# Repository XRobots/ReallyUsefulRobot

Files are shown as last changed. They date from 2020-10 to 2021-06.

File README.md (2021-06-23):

# ReallyUsefulRobot

## Hardware

CAD files are provided in STEP/STP format. This is the whole assembly as a solid format so you can easily edit it. You will need to load it into some CAD software and edit/export individual STLs for printing.

Tyres are printed in TPU, I used Ninjaflex. The rest in PLA printed with a combination of 0.5mm and 1.2mm nozzles.

Motors are 6374 150Kv BLDC motors from the ODrive store: https://odriverobotics.com/shop
Encoders and cables are the 8192 CPR encoders also from the ODrive store.
I used a 56V ODrive 3.6, the robot runs from a 24V LiPo, but it can be 25V+ when it's charged.
Wheel Drive belts are 590mm T5 12mm wide PU belts with steel tensioners made by Synchroflex.
'Utility Stick' drive belt is an HTD 5mm pitch 15mm wide 1790mm length belt.

Other electronics so far include:

-Teensy 4.1
-NVIDIA Xavier NX
-RPLIDAR A2
-24v and 11.1v lipos, switches and wiring etc

## Software

Obviously this isn't a comprehensive guide to ROS, you will need to undestand some core concepts before building this. The Robot runs ROS Melodic on Ubuntu 18.04. This is because the NVIDIA Xavier NX runs 18.04 by default.

On the robot:

The arduino code runs on the Teensy 4.1. This talks to the wheel encoders. It subscribres to the cmd_vel topic and publishes Odom, and TF for the robot's motions. The RPLIDAR A2 node publishes the scan topic: https://github.com/robopeak/rplidar_ros

The Teensy also talks to the ODrive on Serial1. In order to get the ROS Serial library running on the Teensy 4.1, and get both the ROS Serial library and the ODrive library to run together I had to make various modifications. I removed mentions of the Stream Operator which were in the original ODrive Arduino example: https://github.com/madcowswe/ODrive/tree/master/Arduino/ODriveArduino/examples/ I also had to modify the ROS Serial library to add Teensy 4.1 support, and increase buffers so that the Odom message could be published over Serial. I've included both modified libraries as zip files.

The 'rur' and 'rur_description' ROS packages are installed on the robot, and everything is launched with the 'rur_bringup.launch' file. This launches the ROS Serial node to talk tot he Teensy 4.1, starts the laser, and also uses the Robot & Joint State Publishers to publish the transform in the URDF file so the laser is linked to the robot base in the right place.

On my remote workstation:

The 'rur_navigation' ROS package is installed on the remote workstation (although it could be run locally). You will also need to install the ROS navigation stack and slam_gmapping. You will also need to run rosdep to install any other dependencies: http://wiki.ros.org/rosdep

https://github.com/ros-planning/navigation/tree/melodic-devel
https://github.com/ros-perception/slam_gmapping/tree/melodic-devel

There is no launch file for gmapping, so having launched the rur_bringup package on the robot and launched Gmapping ( rosrun gmapping slam_gmapping scan:=scan ) you'll have to open Rviz and manually add/connect the topics for TF/Laser/Map etc. You can use the map server/saver command to save the map ( rosrun map_server map_saver -f ~/map )

After the map is complete you can launch the rur_navigation package which will open Rviz automatically. Use: roslaunch rur_navigation rur_navigation.launch map_file:=$HOME/map.yaml   to connect to the map you saved.

## Simulation

> **_NOTE:_** The following content in the README includes implementation and documentation of Simulation package of ReallyUsefulRobot and is being made by [Pranshu Tople](https://youtube.com/PranshuTople) and is been documented LIVE on his [YouTube Playlist](https://youtube.com/playlist?list=PLFnCFnTZNyU8-omA_VFztWfeFn2gCyY4_). James Bruton is not responsible if the following simulation package has any issues. So if face any problem in simulation, you can open up a GitHub Issue and tag [Pranshu Tople's Github Account](https://github.com/PranshuTople). Hope you enjoy Simulating ReallyUsefulRobot on your PC ☺️✌🏼

<p>
<a href="https://youtu.be/o7w7yv-Nros">
Fusion2URDF</a>
<a href="https://youtu.be/ufYxkNnEFYw">
Teleoperation & Gazebo Plugins</a>
<a href="https://youtu.be/lZVa8o1yxz0">
Mapping in Simulation</a>
<a href="https://youtu.be/DU31PuQjK-I">
Navigation in Simulation</a>
</p>

You don't have to worry anymore if you don't have enough capital to build the RUR robot! You can simply follow the guide given below, and you will have simulation of RUR running on your PC without any issue. The simulation works exactly like the real robot and communicates on the same topic lists. So if you make some software or package for simulated robot, the same would work on real RUR robot without any problem. This opens up gates for the Open-Source community to build various different applications around RUR.

### Downloading Pre-requisites

If you have not downloaded the full-desktop-version of ROS which comes with Gazebo Simulator, then you might need to download a couple of pre-requisites to run the simulation. Even if you have downloaded the full version, yet its a good practice to run the following command which checks if all the pre-requisites are installed or not. And if they are not installed, then the same command downloads them all automatically.

```
sudo apt-get install gazebo9 libgazebo9-* ros-melodic-robot-state-publisher ros-melodic-robot-joint-state-publisher ros-melodic-robot-joint-state-publisher-gui ros-melodic-teleop-twist-keyboard ros-melodic-gmapping ros-melodic-slam-gmapping ros-melodic-map-server
```

### Testing the simulation

Firstly, please place this complete repository or just the ROS folder into your src folder of [catkin_ws](http://wiki.ros.org/catkin/Tutorials) and run catkin_make command. Once the catkin_make is done successfully, then to launch the robot in an empty simulation world for testing in Gazebo Simulator, run the following command on your terminal

```
roslaunch rur_detailed_description gazebo.launch
```
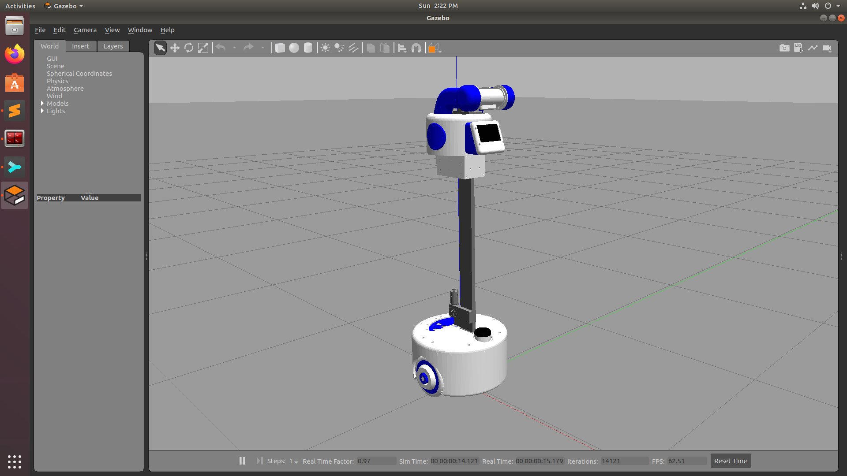
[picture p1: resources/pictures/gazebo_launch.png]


Once you have successfully launched the simulation, you can also run the Teleop node to teleoprate you robot using keyboard. To run the node, paste the following command in a new terminal and you can move your robot around using ' i ' ,' j ' , ' k ' , ' l ' , ' , '<br>
* i = move forward
* k = stop
* j = rotate left
* l = rotate right
* , = move backward
* along with few more operations like 'u','o','m','.' to go forward-left, forward-right, backward-left and backward-right respectively

```
rosrun teleop_twist_keyboard teleop_twist_keyboard.py
```
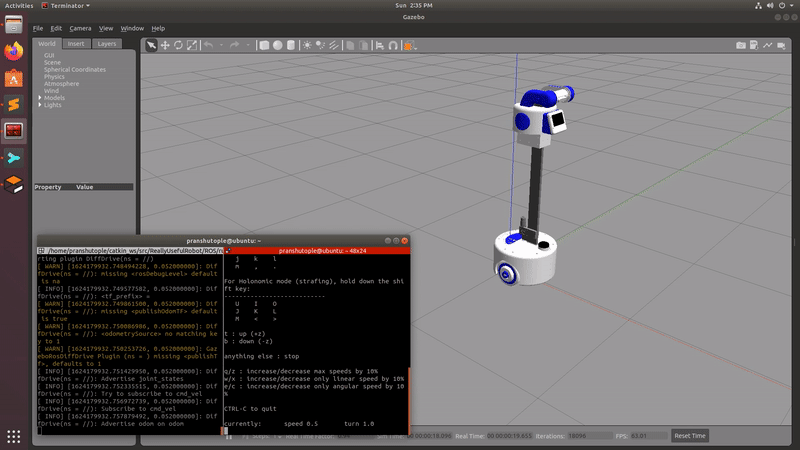
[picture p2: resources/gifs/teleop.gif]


You can also add a couple of obstacles in the environment and check if the LiDAR is able to detect them. Just run the following command and it will open up RViz which is a robot visualization tool that helps you visualize sensor data from the robot.
```
roslaunch rur_detailed_description display.launch
```
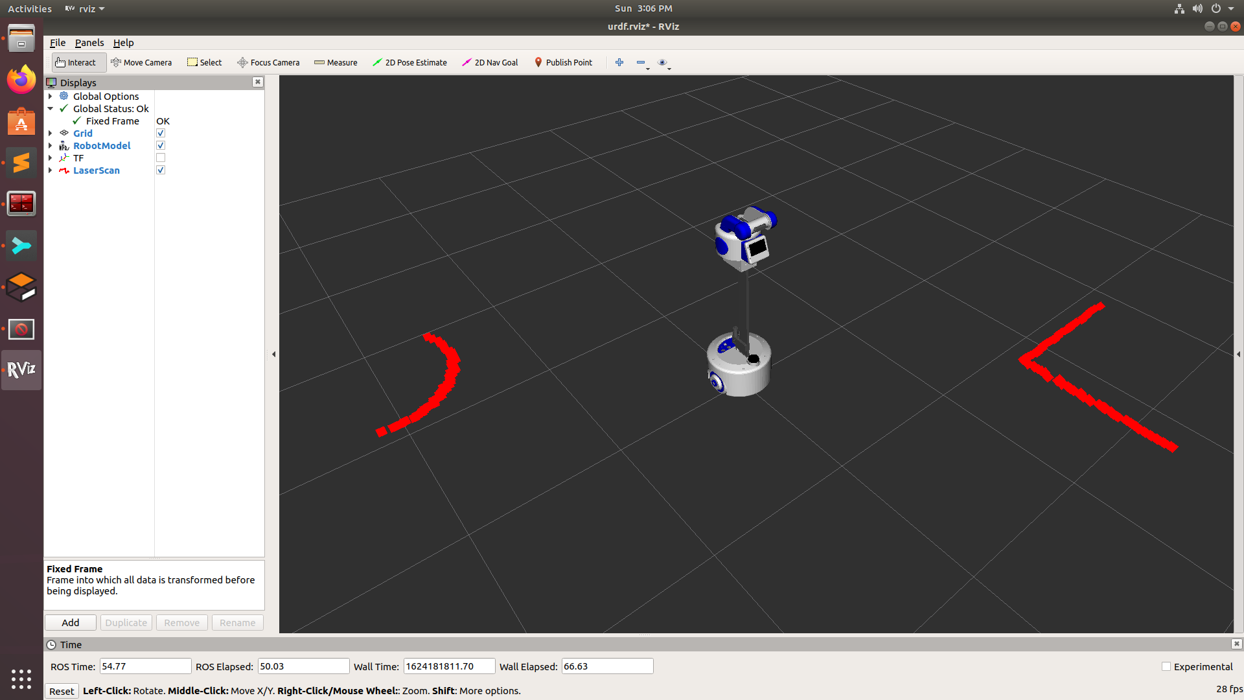
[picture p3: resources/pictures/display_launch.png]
 

RViz is also a place where you can closely inspect the URDF of the robot and look at the detailed TF structer of the robot

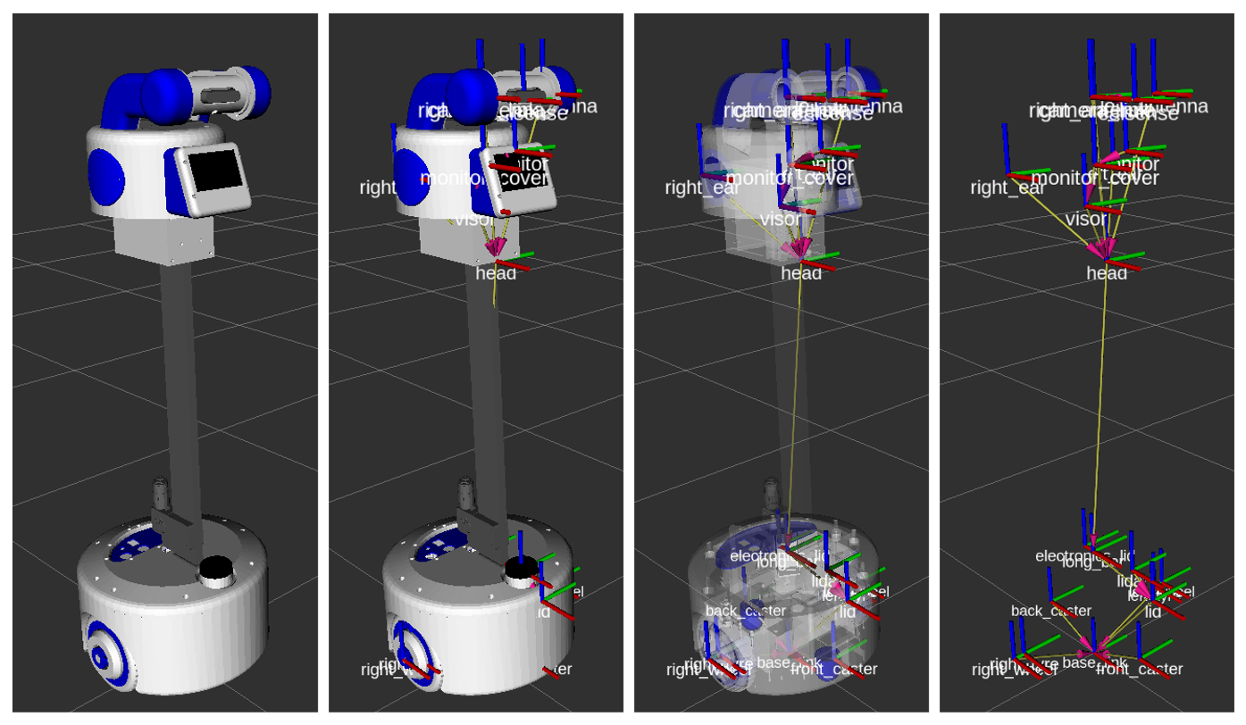
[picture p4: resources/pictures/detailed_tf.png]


### Running the RUR in a simulated world

Once you have tested that both Gazebo and RViz are working properly, then comes the part where you can actually simulate the robot in a virtual world and do mapping and navigation. Just like we run 'rur_bringup.launch' file while working on real robot similarly to start the simulation, we need to launch the 'rur_house.launch' file that will launch gazebo with RUR in a house environment. You can also run 'display.launch' file to view the LiDAR data at the same time. This eleminates the step of manually opening RViz for mapping and setting up different parameters 
```
roslaunch rur_gazebo rur_house.launch
```
```
roslaunch rur_detailed_description display.launch
```
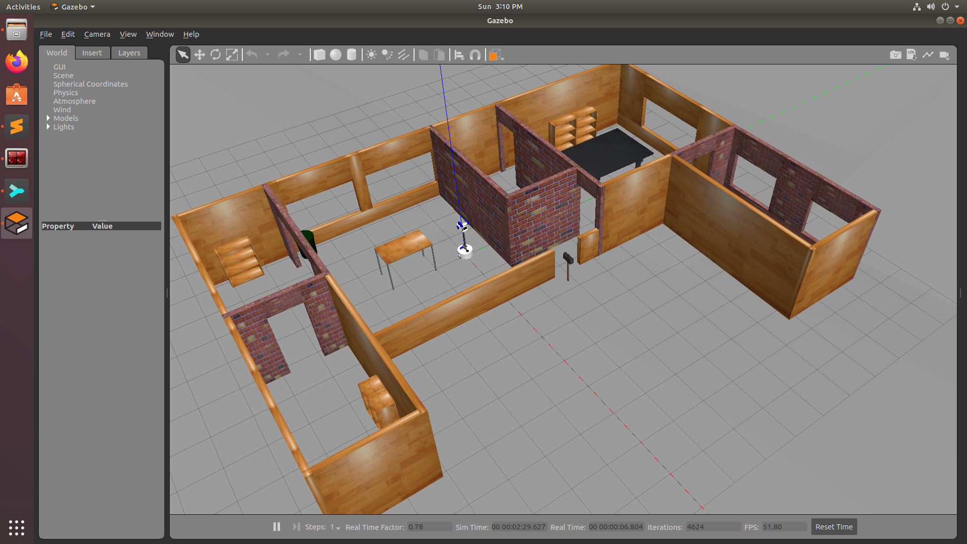
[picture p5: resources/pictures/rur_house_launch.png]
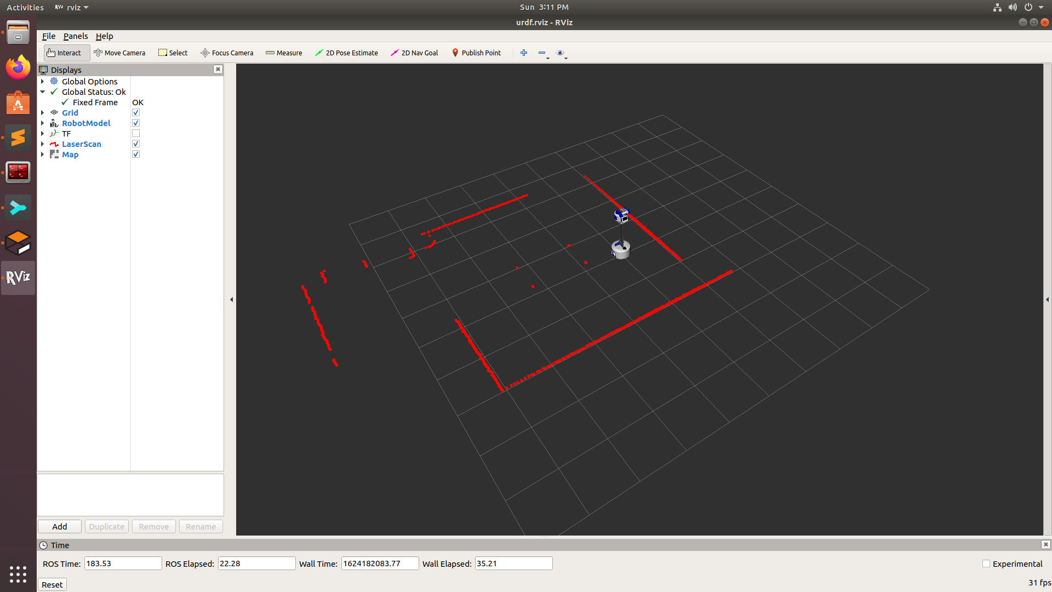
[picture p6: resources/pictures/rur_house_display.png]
 

### Mapping

The command of mapping is the same as the original robot. Just you don't need to open up RViz separetly as you already have 'display.launch' running.
```
rosrun gmapping slam_gmapping scan:=scan
```
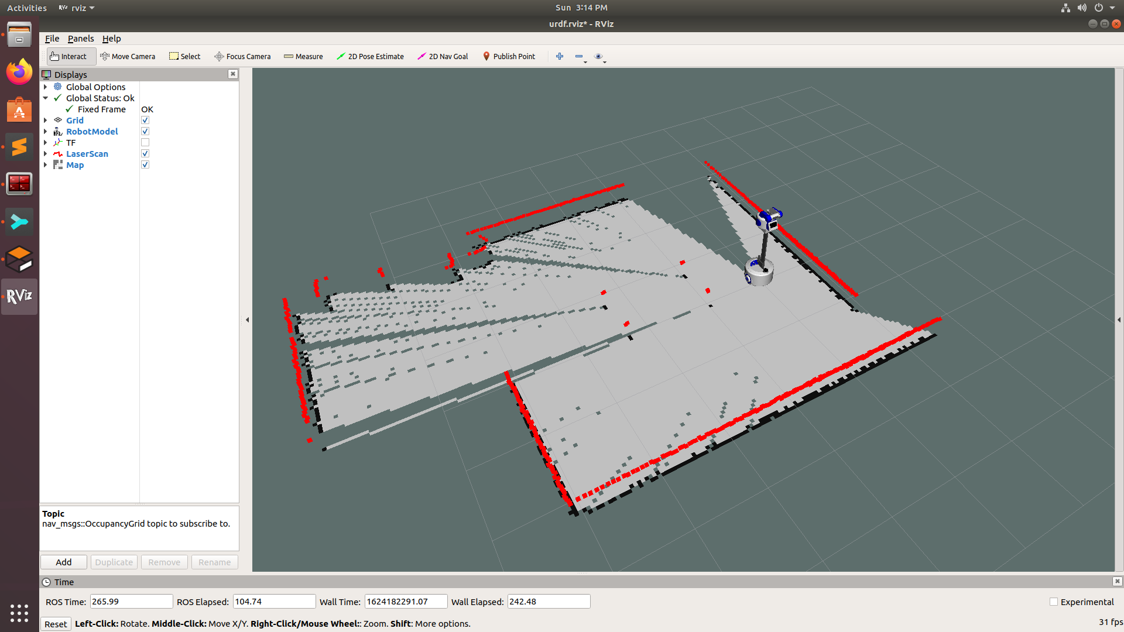
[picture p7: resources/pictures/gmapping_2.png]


Also you can run the teleop node in a separate terminal and move the robot around

 

 

Once you have completed generating the map, before saving the map, navigate to the directory where you want to save the map through your terminal and run the following command to save it.
```
rosrun map_server map_saver -f name_of_map
```
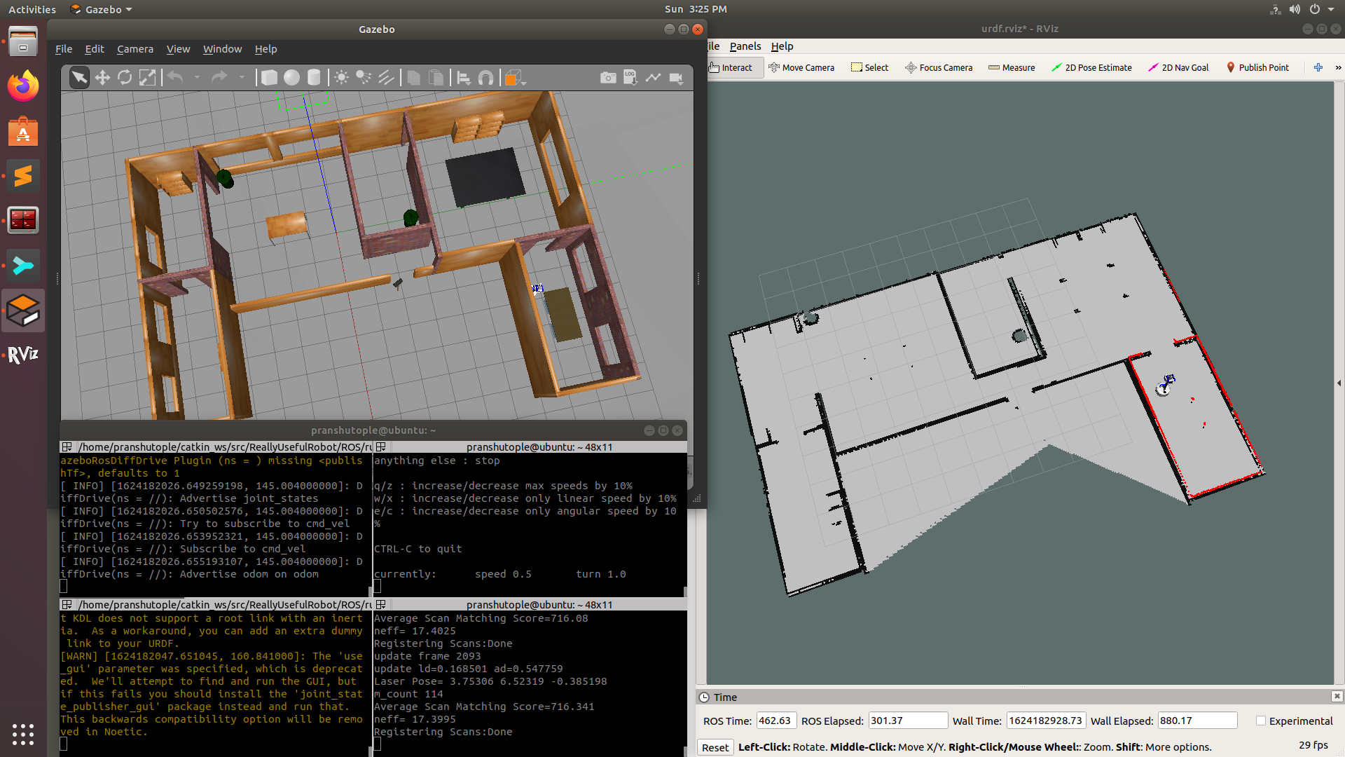
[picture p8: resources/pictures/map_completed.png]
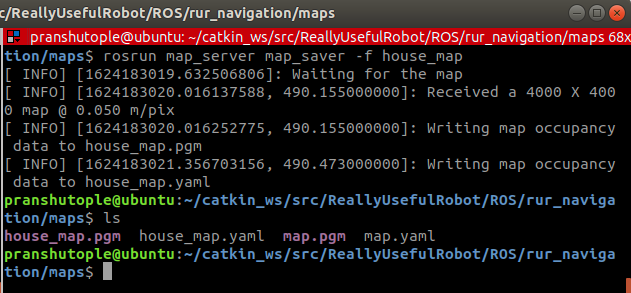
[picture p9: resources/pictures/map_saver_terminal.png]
 

You can then navigate to the directory from your file manager to check if the map is properly saved

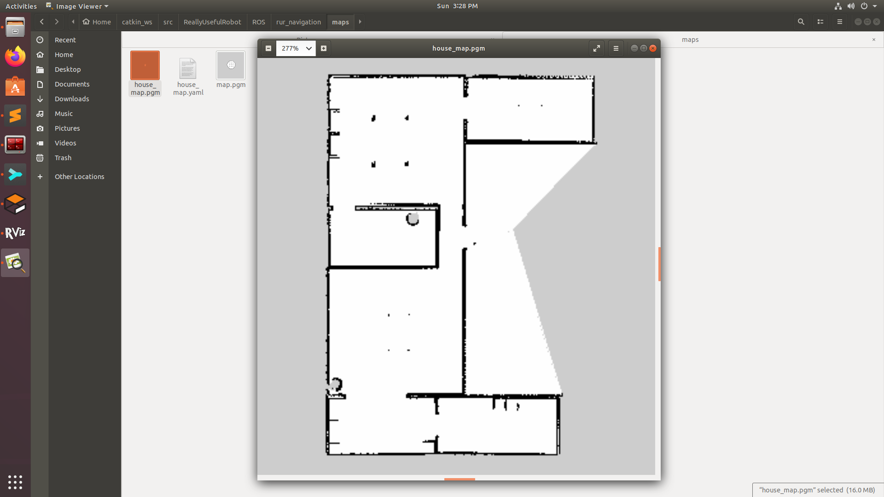
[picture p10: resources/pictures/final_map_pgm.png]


### Navigation

To run naviagtion, firstly you have to make sure that the simulation is running properly. Run the following command to start the simulation
```
roslaunch rur_gazebo rur_house.launch
```
Once you have the simulation running properly with the robot spawned in the middle, now you can run the same navigation file which is used to start navigation on the real robot that is -
```
roslaunch rur_navigation rur_navigation.launch
```
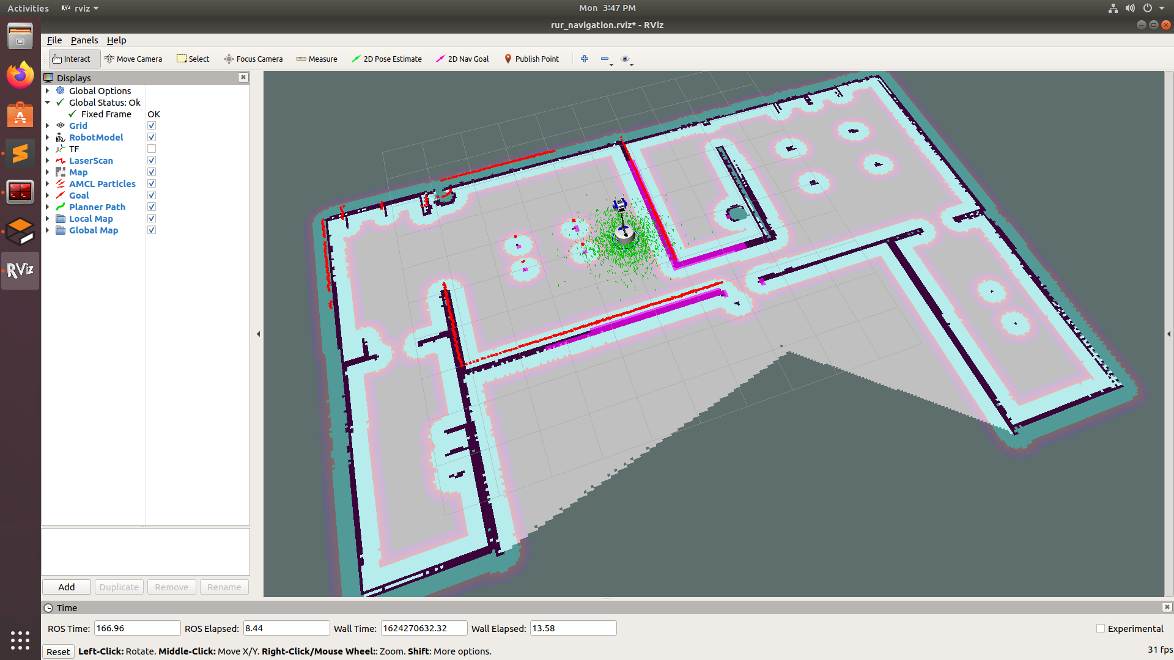
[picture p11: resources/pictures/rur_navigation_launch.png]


But here, you dont need to give any location of the map as the default location of the map is set to the house map. If you want to pass some other map, then you can pass the respective argument. There is no need to launch 'display.launch' as this will start RViz automatically and you can give 2D Nav Goal to the robot

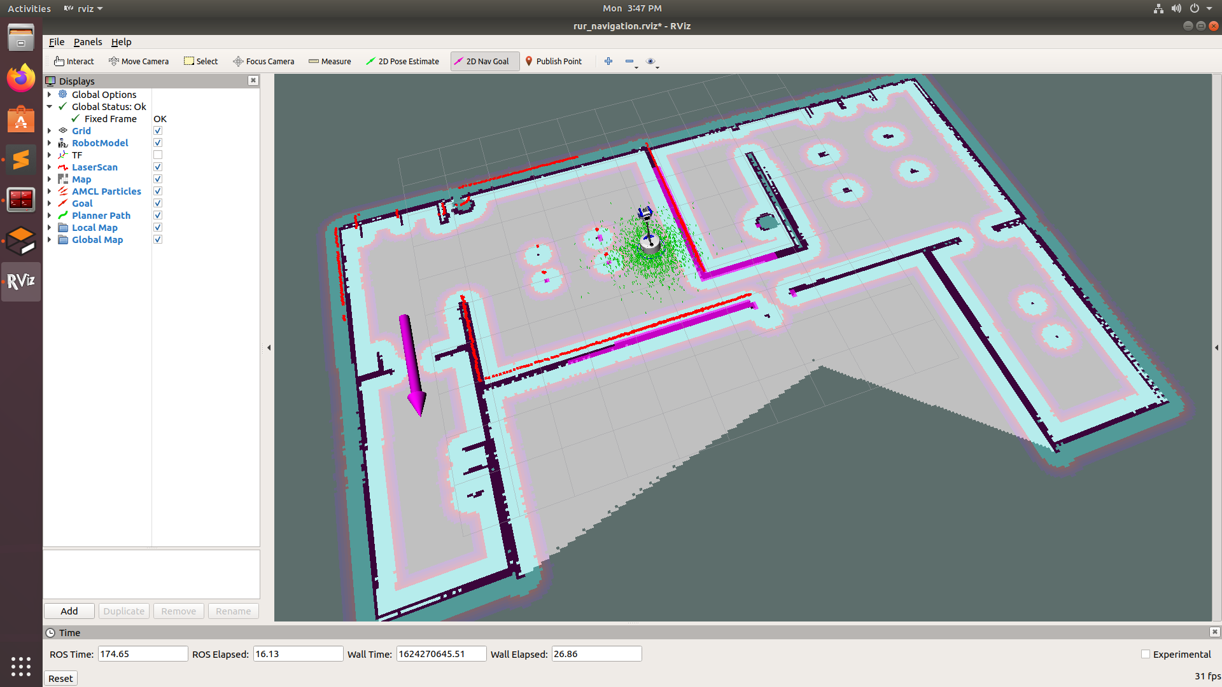
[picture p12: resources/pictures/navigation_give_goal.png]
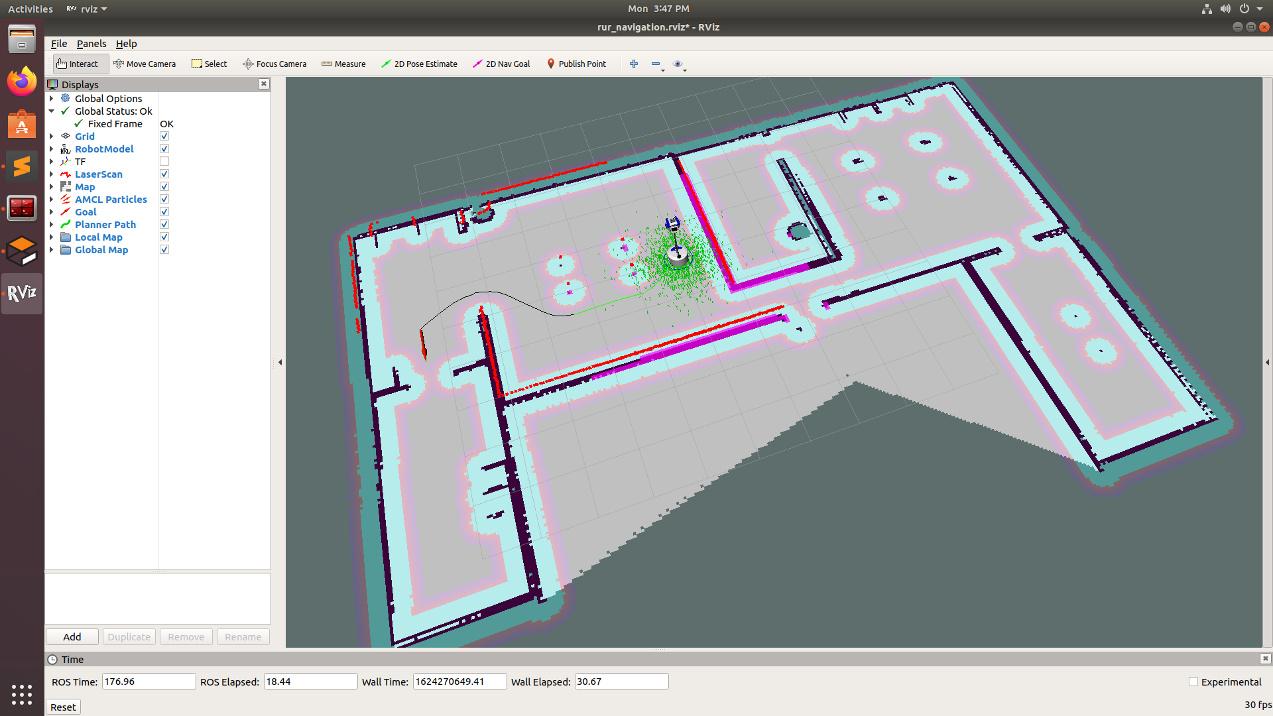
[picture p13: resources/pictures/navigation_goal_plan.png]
 

Once you give the navigation goal, the robot will start navigating to the goal location autonomously in Gazebo and you can visualize that in RViz at the same time. Once you reach the Goal, you will also get a prompt on the terminal that the robot has Reached the Goal...



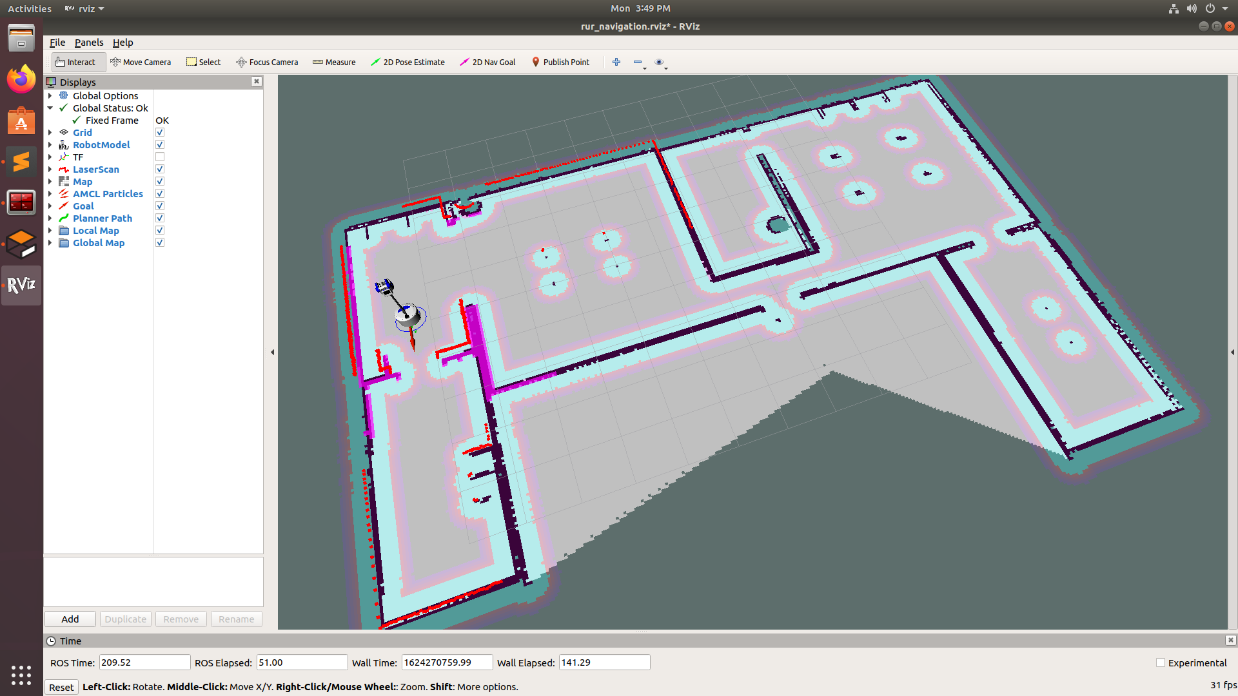
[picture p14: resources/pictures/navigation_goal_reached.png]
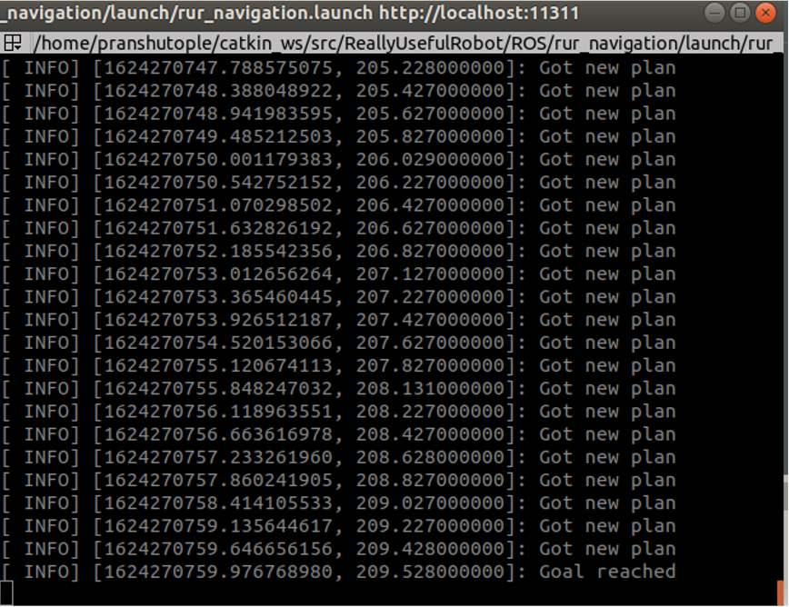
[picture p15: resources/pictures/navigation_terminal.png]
 

Everything related to Simulation you see on this repository was streamed & documented LIVE on Youtube. To Learn more about the Simulation Package in detail and if you wish to see how is it implemented, then check out the following [Playlist on Youtube](https://youtube.com/playlist?list=PLFnCFnTZNyU8-omA_VFztWfeFn2gCyY4_)

If you have any doubts or questions regarding simulation, then either you can comment that on Youtube or else open a Github Issue.

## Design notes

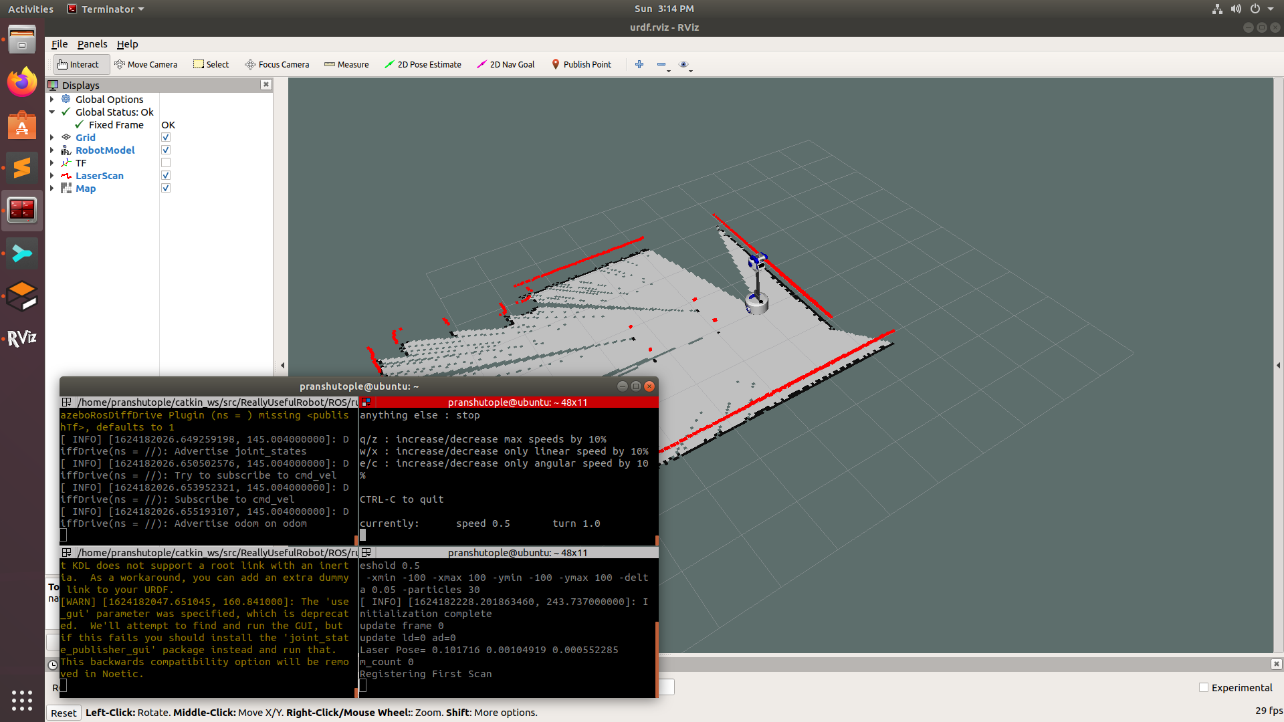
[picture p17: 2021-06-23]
resources/pictures/gmapping_1.png

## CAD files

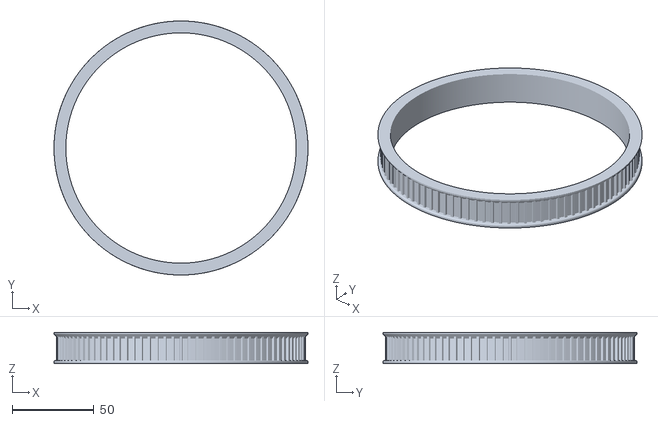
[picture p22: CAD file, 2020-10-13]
CAD/WheelPulley.stl
155.0 x 155.0 x 19.0

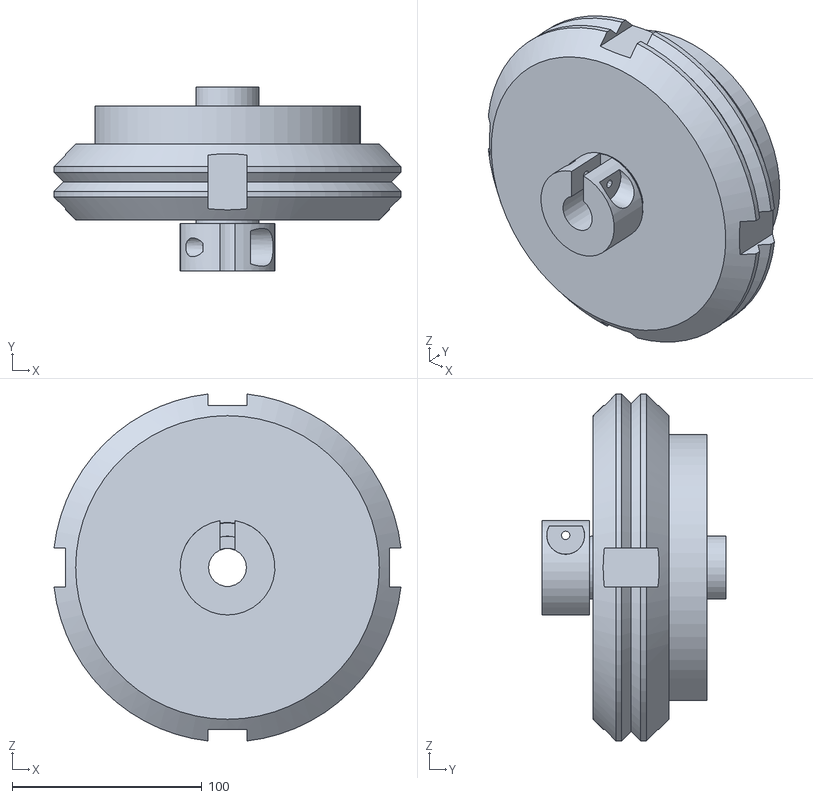
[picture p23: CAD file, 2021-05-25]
ROS/rur_detailed_description/meshes/right_wheel.stl
182.9 x 97.0 x 182.9

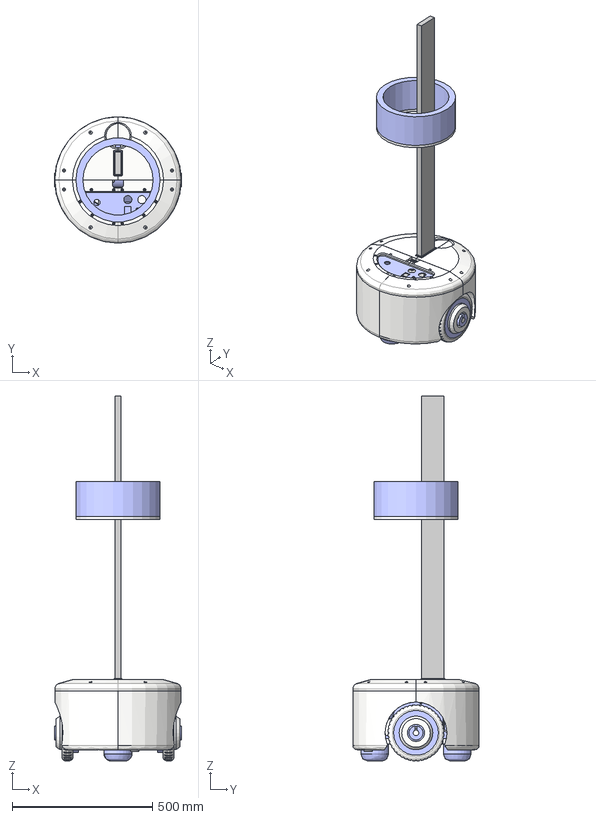
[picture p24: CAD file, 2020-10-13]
CAD/RUR_001.stp
454.0 x 450.0 x 1300.0 mm
wheels
drive
Lid
Top

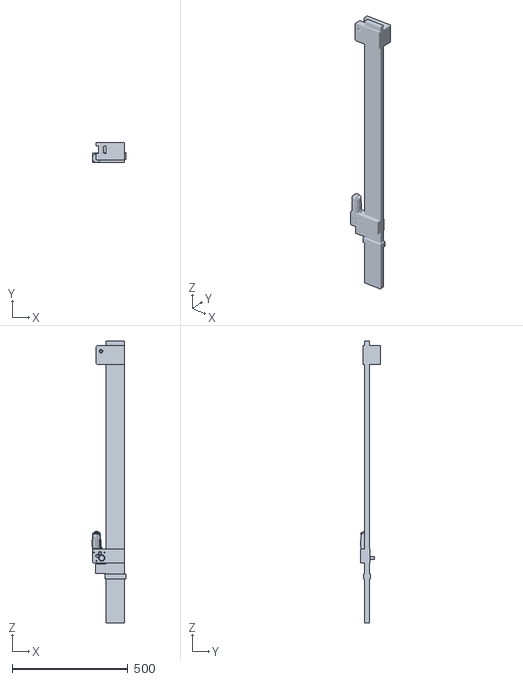
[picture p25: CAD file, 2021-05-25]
ROS/rur_detailed_description/meshes/long_bar.stl
145.3 x 86.0 x 1220.0

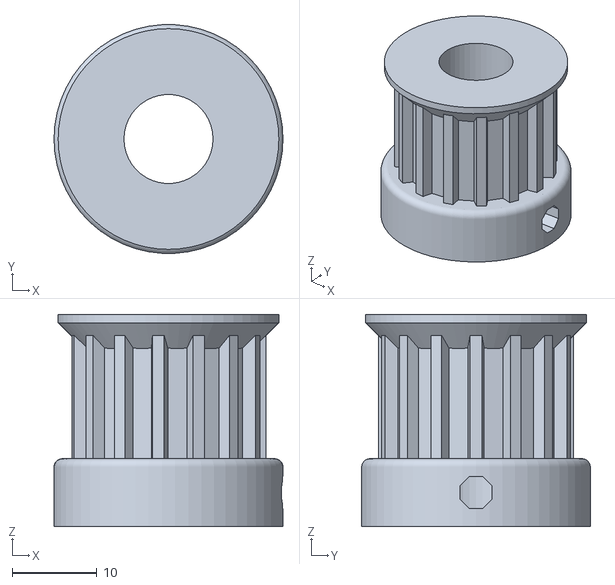
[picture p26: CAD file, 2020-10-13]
CAD/MotorPulley.stl
27.0 x 27.0 x 25.0

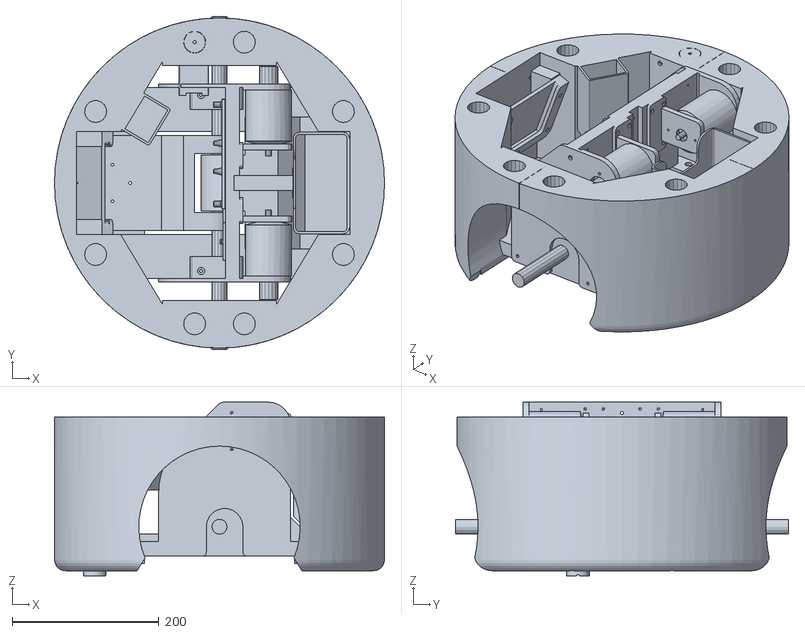
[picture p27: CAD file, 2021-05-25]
ROS/rur_detailed_description/meshes/base_link.stl
450.0 x 454.0 x 237.0

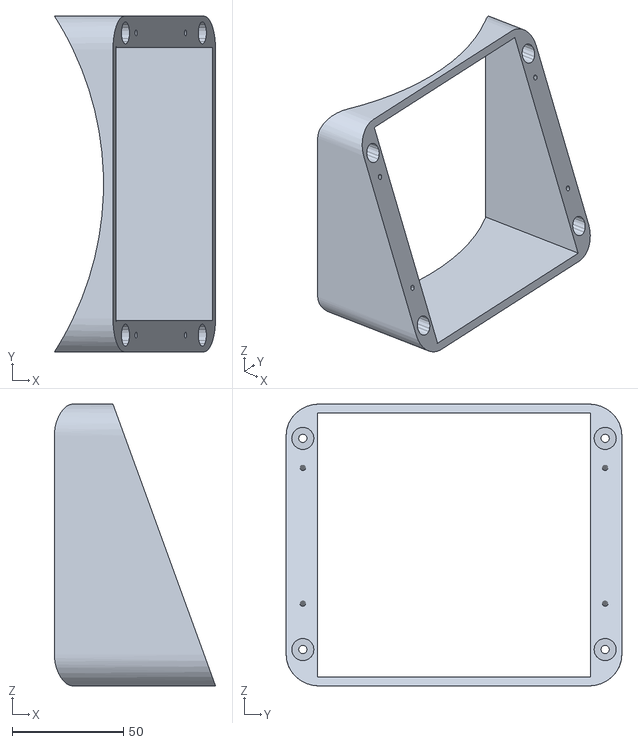
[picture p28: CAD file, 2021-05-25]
ROS/rur_detailed_description/meshes/visor.stl
72.5 x 151.0 x 126.9

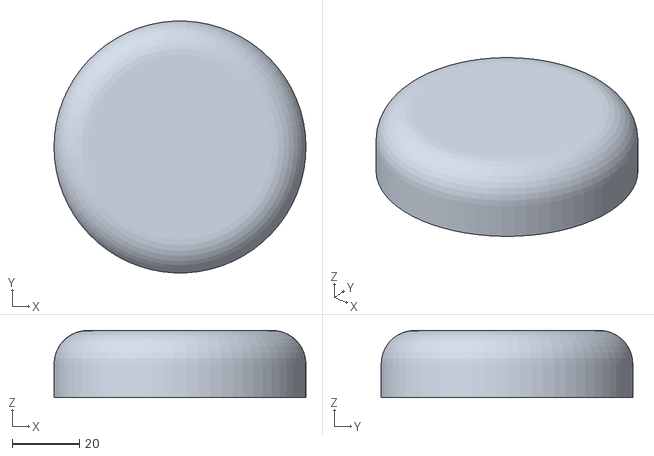
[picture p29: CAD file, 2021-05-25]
ROS/rur_detailed_description/meshes/lidar.stl
75.0 x 74.9 x 20.0

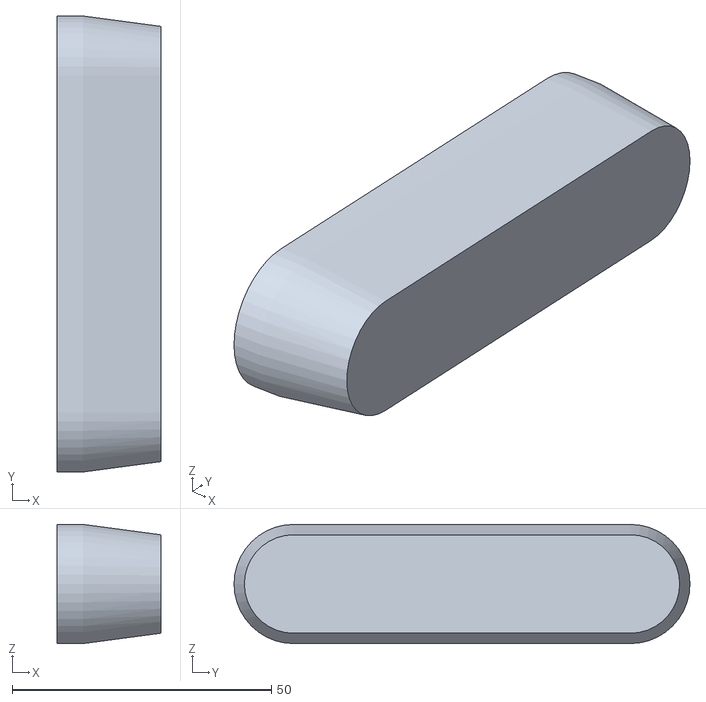
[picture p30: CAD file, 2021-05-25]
ROS/rur_detailed_description/meshes/realsense.stl
20.0 x 88.0 x 23.0

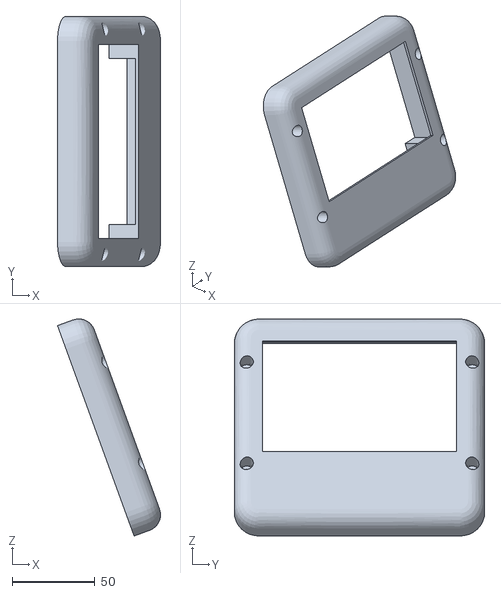
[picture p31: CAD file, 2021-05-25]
ROS/rur_detailed_description/meshes/monitor_cover.stl
62.1 x 151.0 x 130.8

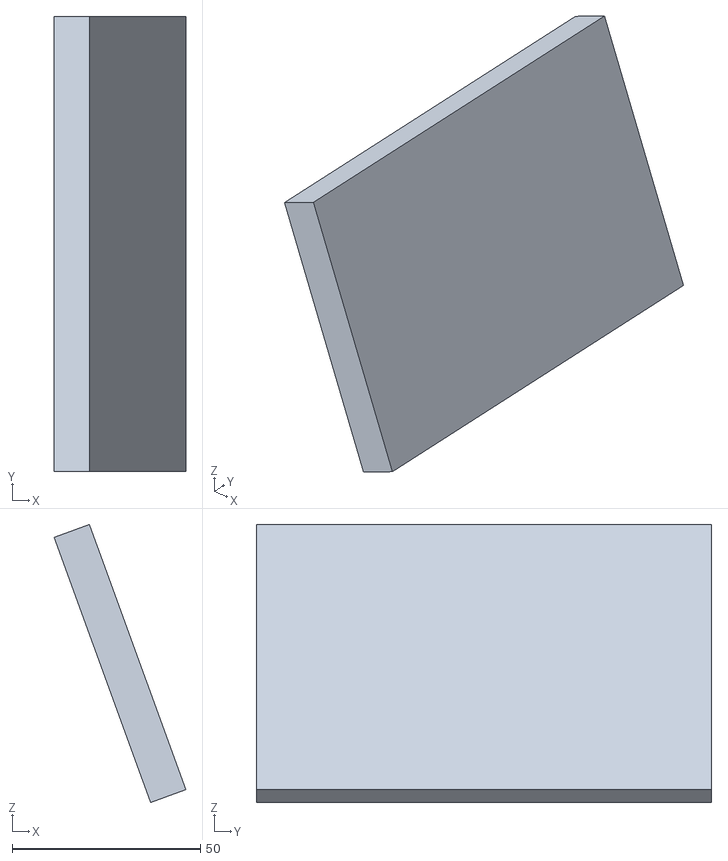
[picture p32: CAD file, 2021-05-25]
ROS/rur_detailed_description/meshes/monitor.stl
35.0 x 121.0 x 73.9

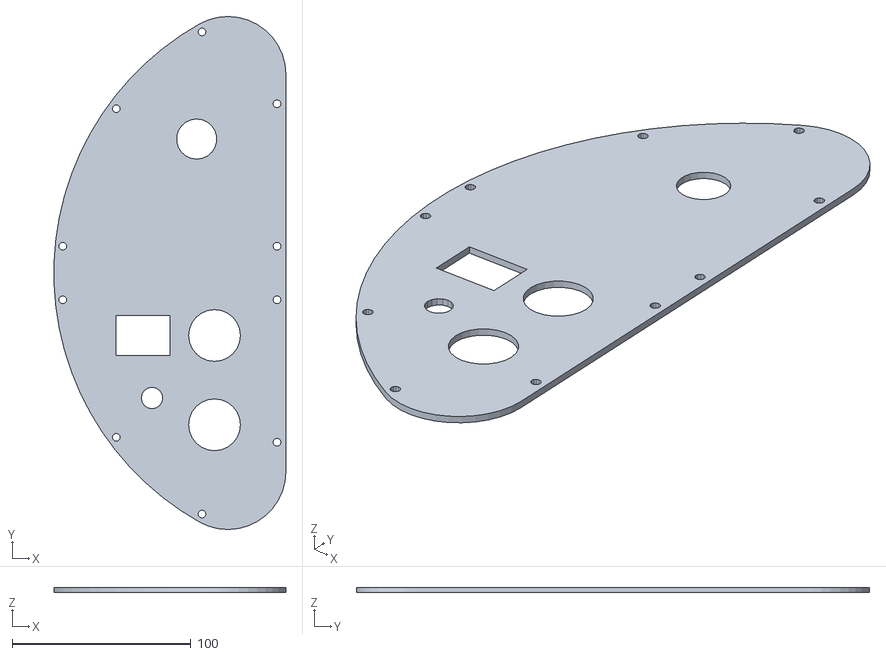
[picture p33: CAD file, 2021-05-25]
ROS/rur_detailed_description/meshes/electronics_lid.stl
129.9 x 287.3 x 3.00

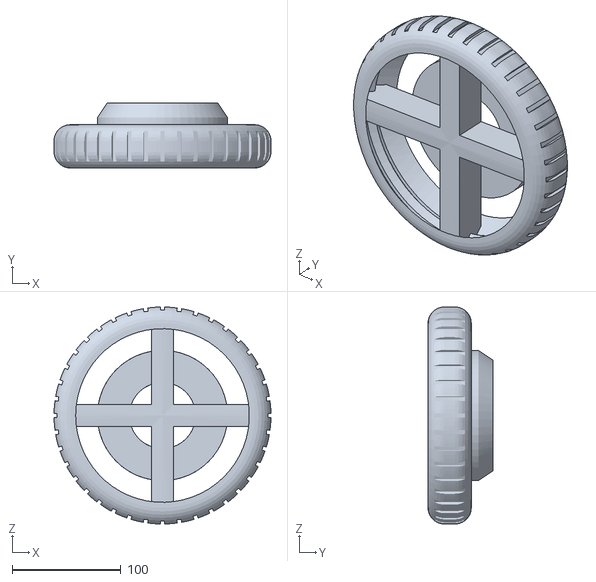
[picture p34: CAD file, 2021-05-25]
ROS/rur_detailed_description/meshes/left_tyre.stl
200.0 x 60.0 x 200.0

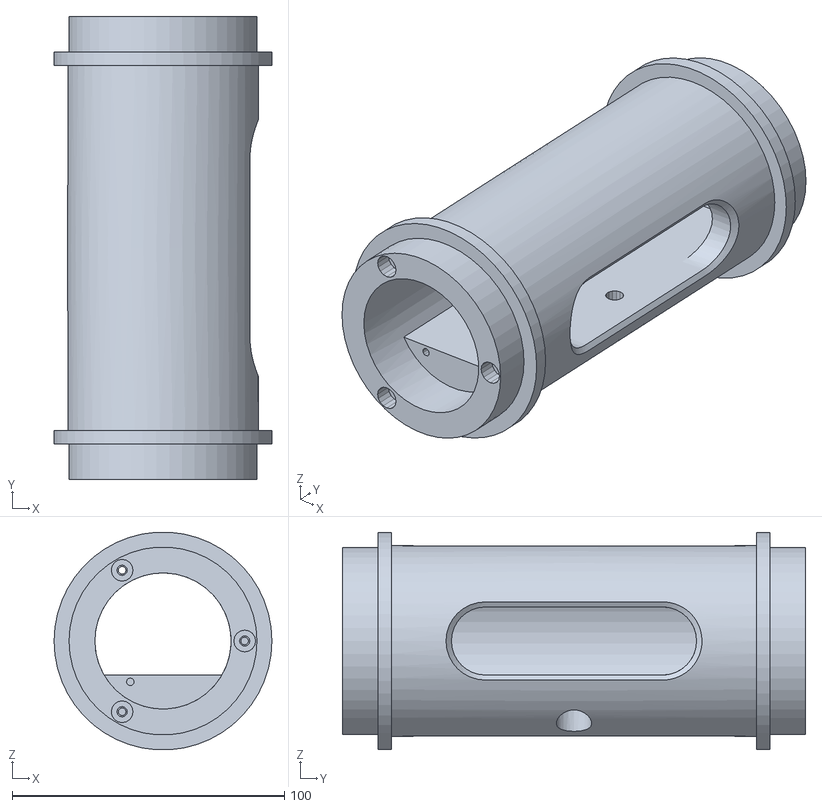
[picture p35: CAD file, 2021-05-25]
ROS/rur_detailed_description/meshes/camera_link.stl
80.0 x 170.0 x 79.8

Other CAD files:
ROS/rur_detailed_description/meshes/left_antenna.stl
ROS/rur_detailed_description/meshes/left_ear.stl
ROS/rur_detailed_description/meshes/lid.stl
ROS/rur_detailed_description/meshes/right_tyre.stl
ROS/rur_detailed_description/meshes/back_caster.stl
ROS/rur_detailed_description/meshes/front_caster.stl
ROS/rur_detailed_description/meshes/head.stl
ROS/rur_detailed_description/meshes/left_wheel.stl
ROS/rur_detailed_description/meshes/right_antenna.stl
ROS/rur_detailed_description/meshes/right_ear.stl

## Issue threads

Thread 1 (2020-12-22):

How to change the Teensy serial port for rosserial

nbaddorf, 2020-12-22:
Hi, I have been working with the RUR programs for a couple of days and they work great! I would like to wire my teensy 4.1 to a raspberry pi for serial, rather than using usb. I tried to follow the rosserial tutorials on changing the wired serial port, but it throws me lots of errors, I am guessing this is because of the modified library. Does anyone know how I could change the teensy serial port used? Thanks!

XRobots, 2020-12-22:
In here: https://github.com/XRobots/ReallyUsefulRobot/blob/main/ROS/rur/launch/rur_bringup.launch  you can change the port name from /dev/ttyACM0 to something else, maybe /dev/ttyUSB0 ?

You may also have to do: sudo chmod 777 /dev/ttyUSB0 to give access.

nbaddorf, 2020-12-22:
Sorry, I guess I didn't explain well enough. I would like to change how the teensy is wired to the raspberry pi. I don't want to use the teensy over usb cable. I would like to wire the teensy to the rpi over serial2.

XRobots, 2020-12-22:
I guess you'd have to hack the rosserial library to use a different serial port.

nbaddorf, 2020-12-22:
I did try to use that, and rosserial actually has a tutorial on how to do that, which I tried, but it gives me errors, due to, I'm guessing, the mods you did the library. Here is the link to that tutorial: http://wiki.ros.org/rosserial_arduino/Tutorials/NodeHandle%20and%20ArduinoHardware

XRobots, 2020-12-22:
Changes I made were to https://github.com/ros-drivers/rosserial/blob/melodic-devel/rosserial_arduino/src/ros_lib/ArduinoHardware.h  to add "defined(__IMXRT1062__)" with the other hardware.

I also modified the buffer size in ros.h as per : https://answers.ros.org/question/73627/how-to-increase-rosserial-buffer-size/

nbaddorf, 2020-12-29:
Ok, thanks! I guess this bug is part of the rosserial library then, not due to the teensy stuff. Thanks for your help, I will keep you posted when I figure out the answer! By the way, I am a huge fan so this is super cool getting to ask for help!

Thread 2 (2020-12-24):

Running navigation stack and Gmapping in On-board raspberry Pi

Zeonsilt06, 2020-12-24:
Hi james. Can i ask you something about this project. Do you run all the Gmapping node and Navigation stack all on Raspberry Pi onboard or some of them in remote computer with SSH ? i also built the same system like you now, but can't figure out why the map update keep missing it's desired rate. I suspect some computation issue, but seeing your video with the same setting as me, it looks all good.

XRobots, 2020-12-24:
No, it's running on a remote workstation. I get that as well, apparently there's a known bug somewhere.

Zeonsilt06, 2020-12-24:
oh so you do the Gmapping Slam and navigation stack in remote workstation , but all serial node and rplidar node is in raspberry pi. Thank you very much !

XRobots, 2020-12-24:
Yep. I did put some notes in the readme about what runs where.

Zeonsilt06, 2020-12-24:
do you have performance issue running node through SSH, like Lidar data delay ?

XRobots, 2020-12-24:
Not that I know of - it seems to work ok

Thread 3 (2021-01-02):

Mounting hole diameters

tom-f-oconnell, 2021-01-02:
I noticed a few holes in the assembly where two parts are joined by a screw have the same inner diameter for the portion the screw should pass through (the clearance portion) as well as the part the screw should be threaded in to. Is this actually how it's printed? I might expect the inner diameter of the part the screw should thread in to to be slightly smaller or something, either to tap the hole or so a screw can self-thread.  Or I might expect the holes-for-threads to be somewhat wider than the clearance holes to accept a heat set insert or something.

Two specific cases I'm looking at now:
- between the 4 walls of the body and each of the plates that connects the pairs of walls together
- between the two halves of the Jetson mount
...there might also be others I'm not seeing right now, but I assume the answer is the same everywhere.

What kinds of fasteners do you use in these cases? Just a screw (self-tapping?), some kind of thread insert, or something else?

Thanks!

XRobots, 2021-01-02:
Sometimes I take a 3mm drill to the one that should be larger. I'm using 2.9mm self tapping countersunk screws.

Closed 2021-01-02.

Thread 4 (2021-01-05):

Consolidated BOM

tom-f-oconnell, 2021-01-05:
Do you think it'd be possible to add a consolidated BOM somewhere? Most of the large non-printed parts, like the major electronic components, are mentioned in the README or in the videos, but there are still some things I'm not sure what / where to buy, such as:
- the springs for the base suspension
- the casters
- the vertical timing belt (and maybe some other components to the vertical drive that I missed)
- fasteners (I know use use 2.9mm self tapping threads in a few places, but it seems there's at least one other kind of fastener)
- the bearings (though I could probably figure this out at least)

I know it might be a bit tedious, especially with the fasteners, but I think it'd be a big help to people trying to recreate this project.

If you want to send me a CSV / spreadsheet / Google Sheet link, I can also help format the BOM as a Github Markdown table if you'd like, perhaps in the README.

Thanks!

XRobots, 2021-01-05:
I've added the vertical belt details to the readme.

The springs I have are actually too tight - they were just some springs I bought off eBay, so you'd be better trying some experimentation here.

The casters are some 50mm ones I had in my spares box, the CAD shows placeholders for the envelope so again, you'd need to see what you can find locally and potentially modify the design to the height correct.

There are a few M4 socket cap bolts in it, but that's about it?

Wheel bearing sizes are shown in the CAD.

Closed 2021-01-05.

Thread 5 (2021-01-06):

TF error

chrismalyon, 2021-01-06:
Hi James,
  Im really struggling with one last bit. When i launch the rur_navigation package on my remote workstation i get two errors "no transform from Laser to Map and no transform from Base_link to Map. Im really stuck, can you point me in the right direction?

Thanks
Chris

XRobots, 2021-01-06:
Presumably you ran Gmapping and made the map ok?

chrismalyon, 2021-01-06:
No as I get a No Map received error but im currently using your map. I have tried to build this robot a few times but havent been able to. I was hoping I could do it now based on your videos but it seems im still struggling :(

XRobots, 2021-01-06:
You'll have to step back a bit. Just run the stuff on the robot and open RVIZ - can you add in the laser scan and TF and have it all line up?  After that you should be able to run Gmapping and have it draw the map.

chrismalyon, 2021-01-06:
Part of the problem i think is finding the correct distro to run. Im running a Raspberry Pi 4 and no matter what distro I use there always seems to be issues with getting ROS running properly. Right now for instance when I run your code I get an error with the serial connection to my Arduino due to a python version issue.

chrismalyon, 2021-01-06:
Ok I figured it out and I now have the robot communicating with the remote workstation and displaying the map correctly. The last bit is driving the robot. if i echo the odom topic and manually turn the wheels im getting the encoder count so that looks good however im not using ODrive im actually using a pair of hoverboard wheels with two BLDC drivers. these are driven essentially by a pwm signal. Im having trouble converting your code to make the wheels move. Below is what i have updated in the main loop. My thinking is to take the forward0 + turn0 and convert this to a PWM value however nothing happens :( I know im taking the micky a bit asking but if you could take a look at the below and let me know what im doing wrong i would appreciate it. I think others would find it useful to see how to make the code work in this way as pwm driven controllers and wheels are a lot cheaper than an ODrive setup.

Thanks in advance
Chris

  nh.spinOnce();        // make sure we listen for ROS messages and activate the callback if there is one

  currentMillis = millis();
  if (currentMillis - previousMillis >= loopTime) {  // run a loop every 10ms
    previousMillis = currentMillis;          // reset the clock to time it

        float modifier_lin = 1.03;        // scaling factor because the wheels are squashy / there is wheel slip etc.
    float modifier_ang = 0.92;        // scaling factor because the wheels are squashy / there is wheel slip etc.

    forward0 = demandx * (83466 * modifier_lin) ; // convert m/s into counts/s
    forward1 = demandx * (83466 * modifier_lin); // convert m/s into counts/s

    turn0 = demandz * (15091 * modifier_ang);    // convert rads/s into counts/s
    turn1 = demandz * (15091 * modifier_ang);    // convert rads/s into counts/s

    //forward1 = forward1 * -1;    // one motor and encoder is mounted facing the other way

//    odrive1.SetVelocity(0, forward0 + turn0);
//    odrive1.SetVelocity(1, forward1 + turn1);

      analogWrite(Left_Wheel_speed, forward0 + turn0);
      digitalWrite(Left_Wheel_Direction, HIGH);
      digitalWrite(Left_Wheel_Stop, HIGH);

      analogWrite(Right_Wheel_speed, forward1 + turn1);
      digitalWrite(Right_Wheel_Direction, LOW);
      digitalWrite(Right_Wheel_Stop, HIGH);

    // get positions and velocities from ODrive

//    pos0 = (odrive1.GetPosition(1)) * -1;
//    pos1 = odrive1.GetPosition(0);

    pos0 = pos;
    pos1 = pos2;

XRobots, 2021-01-07:
Well it looks ok, if you try the motor driver code on its own does it drive the motors?

chrismalyon, 2021-01-07:
It does. I have done some debugging via Serial1 on the arduino mega. It seems that the Arduino is not receiving the cmd_vel topic so there seems to be some issue with how it is subscribing. It is however publishing ok as when i rotate the wheels manually the encoder count is updated to the odom topic which i can see with rostopic echo /odom on the remote workstation. I will continue playing with it to see if I can work out whats going on.

chrismalyon, 2021-01-07:
Hmmm I thought it could be an issue with the Arduino Libraries i was using so I recompiled but didnt work. I have added the following to the callback function on the Arduino but It doesnt seem to fire. If I rostopic echo cmd_vel on the raspberry on the robot then i can see the topic getting the data from rviz but the arduino doesnt seem to capture it :'(

void velCallback(  const geometry_msgs::Twist& vel)
{

  demandx = vel.linear.x;
  demandz = vel.angular.z;

  Serial1.print("Callback X: ");
  Serial1.println(vel.linear.x);

  Serial1.print("Callback Z: ");
  Serial1.println(vel.linear.z);
}

matthewjreeves, 2021-02-09:
Hi chrismalyon

> Ok I figured it out and I now have the robot communicating with the remote workstation and displaying the map correctly.

Earlier in this thread, you had exactly the same problem (above) as I am currently having. Running Rviz after launching all the nodes is throwing up the error Transform [sender=unknown_publisher]
For frame [laser]: No transform to fixed frame [map]. TF error: [Could not find a connection between 'map' and 'laser' because they are not part of the same tree.Tf has two or more unconnected trees.]

I am really stuck too! Could you shed some light on how you fixed it. I am also trying to run it all on an RPI 4b and have had a hell of a time trying to compile Realsense (which is now sorted thankfully)!

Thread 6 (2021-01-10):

Explanation

mazoxBahy, 2021-01-10:
I have the same Odrive controller, but I am building 6-wheeled robot so I have three of them and I am using an Arduino and Jetson Nano as the brain of the robot. I can not publish Odom from Arduino, so  I am sending pos0, pos1 and nh.now() to c++ node running on Jetson and the node on Jetson fix the rest exactly as u do. I get everything working fine but the robot move very fast while it is moving very slow in Rviz and I believe that is because u are using different wheel size and so on. But I can not see where u input ur wheel size and wheel separation and so on. I am wondering if you can point out where u do that and if you can explain quickly what is the values 83466,15091 and 83.44 respectively in lines 112, 115 and 135.

XRobots, 2021-01-10:
It's in the Arduino code based on the encoder counts - basically the lines you pointed out.

I put all the details & calcs here: https://github.com/XRobots/ReallyUsefulRobot/blob/main/wheelReduction.txt

mazoxBahy, 2021-01-13:
Thanks for the quick response. I have been checking and testing with the calculation you refered to. But it I am doing something wrong which I can not figure out. The robot is going into the same directions in RVIZ but not with same amount. The real robot might go for 5 meters which should correspond to  5 squares in RVIZ but in RVIZ , it is showing so much less than that in RVIZ. I have hoverboard motors which are the wheels by them self. Wheel diameter is 6.5 inches =165.1 mm. And the ROBOT_WIDTH is 480 mm.

Here is my Arduino code part:

/*A node which subscribing /cmd_vel coming from keyboard(teleop node)
               Publishing  /pos containing info about the position(encoder) of left/right rear motors.
         
*/
#include <HardwareSerial.h>
#include <ODriveArduino.h>
#include <Wire.h>
#include <ros.h>
#include <std_msgs/String.h>
#include <geometry_msgs/Vector3Stamped.h>
#include <geometry_msgs/Twist.h>
#include <ros/time.h>

#define ROBOT_WIDTH (480) //MILLI METER
#define WHEEL_DIAMETER (330.2)  // MILLI METER
#define WHEEL_CIRC (518.676947108) //circumference OF THE WHEEL
#define CPR_ENCODER (90)

/*
Driving forward
1 revolution= WHEEL_CIRC = 518.676947108 mm
Each mm travelled is CPR_ENCODER/WHEEL_CIRC = 90/518.676947108 =0.1735184116 counts per mm
Then each meter travelled is 0.1735184116*1000=173.5184116 counts per meter
Then each meter/sec= 173.5184116 counts/sec

Turning:
2pi radians = 360'  and  pi radians = 180'
distance each wheel has to go to travel 180' = (ROBOT_WIDTH*pi)/2=753.982236862 mm=pi radians
753.982236862 mm=1.45366444579 revolution=130.829800121 encoder counts=pi radians

1 radian = 130.829800121/pi=41.644418786 encoder counts
*/

HardwareSerial& odrive_serial1 = Serial1;
HardwareSerial& odrive_serial2 = Serial2;
HardwareSerial& odrive_serial3 = Serial3;
//axis0(M0)-left
//axis1(M1)-right
ODriveArduino odrive1(odrive_serial1);
ODriveArduino odrive2(odrive_serial2);
ODriveArduino odrive3(odrive_serial3);

// cmd_vel variables to be received to drive with
float demandx;
float demandz;

// timers for the sub-main loop
unsigned long currentMillis;
long previousMillis = 0;    // set up timers
float loopTime = 10;
long forward0;
long forward1;
long turn0;
long turn1;

// position and velocity variables read from the ODrive
long pos0;
long pos1;

long pos0_old;
long pos1_old;
long pos0_diff;
long pos1_diff;
float pos0_mm_diff;
float pos1_mm_diff;

ros::NodeHandle nh;

//function that will be called when receiving command from host
void handle_cmd (const geometry_msgs::Twist& cmd_vel) {
                                           
     demandx = 0.02*cmd_vel.linear.x; //decrease by 98%
     demandz = 0.02*cmd_vel.angular.z; //decrease by 98%
}

ros::Subscriber<geometry_msgs::Twist> cmd_vel("cmd_vel", handle_cmd);   //create a subscriber to ROS topic for velocity commands (will execute "handle_cmd" function when receiving data)
geometry_msgs::Vector3Stamped pos_msg;                                //create a "pos_msg" ROS message
ros::Publisher pos_pub("pos", &pos_msg);                          //create a publisher to ROS topic "pos" using the "pos_msg" type

void setup() {

  nh.initNode();                            //init ROS node
  nh.getHardware()->setBaud(115200);         //set baud for ROS serial communication
  nh.subscribe(cmd_vel);                    //suscribe to ROS topic for velocity commands
  nh.advertise(pos_pub);                  //prepare to publish speed in ROS topic
  odrive_serial1.begin(115200);
  odrive_serial2.begin(115200);
  odrive_serial3.begin(115200);
  odrive1.SetVelocity(0,0);
  odrive1.SetVelocity(1,0);
  odrive2.SetVelocity(0,0);
  odrive2.SetVelocity(1,0);
  odrive3.SetVelocity(0,0);
  odrive3.SetVelocity(1,0);
  odrive1.SetPosition(0,0.0);
  odrive1.SetPosition(1,0.0);
  odrive2.SetPosition(0,0.0);
  odrive2.SetPosition(1,0.0);
  odrive3.SetPosition(0,0.0);
  odrive3.SetPosition(1,0.0);
  Serial.begin(115200);
  while (!Serial) ;

}

//_________________________________________________________________________

void loop() {
  nh.spinOnce();
  currentMillis = millis();
  if (currentMillis - previousMillis >= loopTime) {  // run a loop every 10ms  
     previousMillis = currentMillis;          // reset the clock to time it
     float modifier_lin = 1.03;        // scaling factor because the wheels are squashy / there is wheel slip etc.
     float modifier_ang = 0.92;        // scaling factor because the wheels are squashy / there is wheel slip etc.

     forward0 = demandx * (173.5184116 * modifier_lin) ; // convert m/s into counts/s
     forward1 = demandx * (173.5184116 * modifier_lin); // convert m/s into counts/s

     turn0 = demandz * (41.644418786 * modifier_ang);    // convert rads/s into counts/s
     turn1 = demandz * (41.644418786 * modifier_ang);    // convert rads/s into counts/s

      forward1 = forward1*-1;      // one motor and encoder is mounted facing the other way
     odrive1.SetVelocity(1, forward0 + turn0); //-1 the motors are on opposite direction
     odrive1.SetVelocity(0, forward1 + turn1);
     odrive2.SetVelocity(1, forward0 + turn0); //-1 the motors are on opposite direction
     odrive2.SetVelocity(0, forward1 + turn1);
     odrive3.SetVelocity(1, forward0 + turn0); //-1 the motors are on opposite direction
     odrive3.SetVelocity(0, forward1 + turn1);

     // get positions from ODrive
      pos1 = (((odrive1.GetPosition(0)) *-1)+((odrive2.GetPosition(0)) *-1)+((odrive3.GetPosition(0)) *-1))/3.0;           
      pos0 = (odrive1.GetPosition(1)+odrive2.GetPosition(1)+odrive3.GetPosition(1))/3.0;
      // work out the difference on each loop, and bookmark the old value
    pos0_diff = pos0 - pos0_old;
    pos1_diff = pos1 - pos1_old;    
    pos0_old = pos0;
    pos1_old = pos1;

    // calc mm from encoder counts
    pos0_mm_diff = pos0_diff /0.1735184116;
    pos1_mm_diff = pos1_diff /0.1735184116;

     publishPos();
  }
 }

void publishPos() {
  pos_msg.header.stamp = nh.now();      //timestamp for odometry data
  pos_msg.vector.x = pos0_mm_diff;
  pos_msg.vector.y = pos1_mm_diff;   
  pos_pub.publish(&pos_msg);
  nh.spinOnce();
}

XRobots, 2021-01-13:
Maybe multiply the number by 5 then?

mazoxBahy, 2021-01-14:
Does not seems as a solution for the problem but another question is that : "forward0 = demandx * (173.5184116 * modifier_lin) ; // convert m/s into counts/s". So according to my understading u assume that setVelocity() takes ticks per second because that is what you are sending. While according to "https://docs.odriverobotics.com/ascii-protocol" the velocity is "the desired velocity in [turns/s]" which is different to the ticks/s you sending.  Is not turn/s the revolution/s?

XRobots, 2021-01-14:
turns/s is in the new ODrive firmware that's just been released. I'm using the old firmware which is counts/s

mazoxBahy, 2021-01-14:
Ok, but then that is why I have problems with it. Do you recommend me to use an old firmware or should I change the code to work with turns/s instead? Does the getposition in old firmware returns counts? becuase the new one returns turns which means 1.3 revloution is detected as one revolution and so on.

XRobots, 2021-01-14:
Yes it returns counts. It's up to you I guess, I haven't tried using the new firmware yet.

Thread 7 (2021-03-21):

Tire TPU infill

tom-f-oconnell, 2021-03-21:
What infill did you print your TPU tires with?

Googling around it seems like the 85A hardness Ninjaflex is the most common (and perhaps also the only one called *just* "Ninjaflex", but I'm not sure). Do you know whether this is also the hardness of the Ninjaflex you used?

Thanks again.

XRobots, 2021-03-21:
Yep that's the one - just the standard stuff. It was 4 perimeters and around 40% infill - whatever made each tyre come out of one roll of filament basically. Previously I've used up to 80% infill for tyres which is practically solid.

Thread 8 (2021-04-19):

the robot moves faster in rviz then in real

bilx6043, 2021-04-19:
hi... thanks for all the hardwork you put on this project and make it working.. i try your code with my robot using audriuino mega..but my robot runs faster in rviz then in real .. and i think cuz of that the navigation stack also not work..i have tried the wheel reduction ratio part and calculate the values according to my robot but still no luck..

XRobots, 2021-04-19:
The ODrive firmware has been updated since I built this to use 'turns' instead of encoder counts as the units. So the amount the wheels turn will need rescaling.

bilx6043, 2021-04-20:
thanks for the reply... so that is the issue... i am using your audrino code to connect to odrive... i have calculated the wheel revolution and put it on the code... i have calculated check revolution per second with speed and its ok.. not when i send speed from keyboard, lets say 0.5 .. on the odom topic i got different speed its 9.5 .. so i think its cuz of the odive firmware update causing the issue or i am missing something?

abdullahkose20, 2021-04-20:
Hi.. bruton
 ı have studied on ros and odrive for around 6 mounths. I appreciate your studies. Previously, we didnt have anyproblem about controlling odrive and ros but now, due to odrive update firmware, we faced same problem. My robot worked stable before, now it is unstable and so ı can not reach my targets. Can u help me with update version of odrive. thanks for your answer

XRobots, 2021-04-20:
Yep here's the ODrive migration guide to the new firmware: https://docs.odriverobotics.com/migration

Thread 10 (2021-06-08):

Some tips on ROS

mintar, 2021-06-08:
Cool project! I watched your [video](https://www.youtube.com/watch?v=CsVCffDxwk8) and really enjoyed it. While watching, I noticed that I've seen several other of your videos over the years and liked them a lot.

Your skills in many areas surpass my own by far. However, since I've been developing ROS software for a living for 10 years, this is one area where I figured I could help, and I couldn't resist giving you some unsolicited advice, so here goes.

### Aligning depth and color images

Instead of this hackery:

https://github.com/XRobots/ReallyUsefulRobot/blob/8775ac270d4725912ffaa4dbddf5a0fcf3746b91/Vision/camera11_depth.py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

... you should either use `pyrealsense2.rs2_project_color_pixel_to_depth_pixel`, or perhaps better yet don't use the `pyrealsense2` library, but instead use the `realsense2_camera` ROS driver something like this (adjust width + height as needed):

```xml
<include file="$(find realsense2_camera)/launch/rs_rgbd.launch">
  <arg name="camera"          value="d435" />

  <arg name="depth_width"     value="848"/>
  <arg name="depth_height"    value="480"/>
  <arg name="enable_depth"    value="true"/>

  <arg name="infra_width"     value="848"/>
  <arg name="infra_height"    value="480"/>
  <arg name="enable_infra1"   value="true"/>
  <arg name="enable_infra2"   value="true"/>

  <arg name="color_width"     value="848"/>
  <arg name="color_height"    value="480"/>
  <arg name="enable_color"    value="true"/>

  <arg name="enable_sync"     value="true"/>
  <arg name="align_depth"     value="true"/>
</include>
```

From the [realsense-ros README](https://github.com/IntelRealSense/realsense-ros):

> **align_depth**: If set to true, will publish additional topics for the "aligned depth to color" image.: `/camera/aligned_depth_to_color/image_raw`, `/camera/aligned_depth_to_color/camera_info`.

Since we set the `camera` parameter to `d435`, this will be  `/d435/aligned_depth_to_color/image_raw` instead.

Then you can use a [TimeSynchronizer](http://wiki.ros.org/message_filters#Example_.28Python.29-1) to subscribe to the `/d435/aligned_depth_to_color/image_raw` and `/d455/color/image_raw` topics, and they will be aligned pixel-by-pixel; in other words, the depth image will be transformed to look as if the depth camera was exactly at the RGB camera's position and also as if it had the same camera parameters (lens distortion etc.) as the RGB camera.

### Removing lens distortion

There should also be two topics called `.../image_rect_raw` and `.../image_rect_color`. These are the *rectified* topics, i.e. any lens distortion has been removed. You should use those if you're going to use some trigonometry like you showed in the video, but I'll show you a better way below.

### Using TF

Regarding the trigonometry calculations, you can make your life *much* easier by using the `tf2_ros` library. There are [some tutorials](http://wiki.ros.org/action/show/tf2/Tutorials?action=show&redirect=tf2_ros%2FTutorials) that are 100% worth going over. TF is one part where ROS really shines.

In short, you should:

* Remove the `joint_state_publisher` from your `rur_bringup` launch file.
* Publish the angle of the camera tilt unit as a [`sensor_msgs/JointState`](http://docs.ros.org/melodic/api/sensor_msgs/html/msg/JointState.html) message on the topic `/joint_states` instead of a `std_msgs/UInt16` as you're doing now. You can leave the `velocity` and `effort` fields empty, just fill in the `name` field with the name of the joint in the URDF and the `position` field with the joint angle in radians.
* Do the same for the wheel joints. The `joint_states` topic can have multiple independent publishers, they don't all need to be in one message.
* Add the arm to your URDF and also publish `joint_states` for them.

This will allow the `robot_state_publisher` to pick up the actual joint states from your robot, display them in RViz and (most importantly) publish correct TFs for them.

Now is where the magic happens: You can now automatically transform the center point of your cup into any frame (`base_link`, or your gripper frame, or whatever). Disclaimer: I haven't tested the code below, but it should give you the right ideas:

```python
import rospy
import message_filters
import tf2_geometry_msgs
import tf2_ros

from image_geometry import PinholeCameraModel

from geometry_msgs.msg import PointStamped
from sensor_msgs.msg import Image, CameraInfo

class MyNode(object):
    def __init__(self):
      camera_model = PinholeCameraModel()

      self.tf = tf2_ros.Buffer()
      self.tfl = tf2_ros.transform_listener.TransformListener(tf)

      self.color_image_sub = message_filters.Subscriber('/d455/color/image_raw', Image)
      self.depth_image_sub = message_filters.Subscriber('/camera/aligned_depth_to_color/image_raw', Image)
      self.info_sub = message_filters.Subscriber('/d455/color/CameraInfo', CameraInfo)

      self.ts = message_filters.TimeSynchronizer([color_image_sub, depth_image_sub, info_sub], 10)
      self.ts.registerCallback(callback)

    def callback(color_image, depth_image, camera_info):
      # TODOs:
      # - compute detectX, detectY as in previous code
      # - look up detectZ for those pixel coordinates from depth image

      # compute 3D point (in camera frame)
      camera_model.fromCameraInfo(camera_info)
      camera_model.projectPixelTo3dRay((detectX, detectY))
      (x, y, z) = camera_model.projectPixelTo3dRay((detectX, detectY))
      p = PointStamped()
      p.header = camera_info.header
      p.point.x = x * detectZ
      p.point.y = y * detectZ
      p.point.z = detectZ

      # automagically transform into any frame
      tf.transform(p, 'base_link')

def main():
    rospy.init_node('vision')
    try:
        rospy.spin()
    except rospy.ROSInterruptException:
        pass

if __name__ == "__main__":
    main()
```

### Controlling the arm

If you want to go in really deep, look at [MoveIt](https://moveit.ros.org/). It's not going to be easy though!

### Joint state publisher GUI

Bonus tip: If you use the `joint_state_publisher_gui` in your `display.launch` like this...

```xml
  <node name="joint_state_publisher_gui" pkg="joint_state_publisher_gui" type="joint_state_publisher_gui"/>
```

..., it will pop up a little GUI where you can play around with the joints in your URDF. Very useful for debugging.

XRobots, 2021-06-08:
Thanks Martin,

I'm not using a ROS camera driver. How do I align the images with the NVIDIA Jetson Inference deep learning code camera feed?

mintar, 2021-06-08:
> I'm not using a ROS camera driver.

Yes, but why not? It's really useful. For example, you can use the camera image in other ROS nodes, display it in RViz and so on.

> How do I align the images with the NVIDIA Jetson Inference deep learning code camera feed?

Looking at your code, you currently do the following:

```python
img, width, height = camera.CaptureRGBA()
detections = net.Detect(img, width, height)
```

The first line retrieves the image in `img`, the second line passes it to the neural net. So all you need to figure out is how to convert the ROS message `color_image` in my code into the same format that `img` uses. Unfortunately I don't know what that format is; I guess an array of floats, or an array of array of floats or something. It would be helpful to put a `print img` and `print type(img)` into the code temporarily to figure that out.

If you're lucky, you could do it like this:

```
from cv_bridge import CvBridge

# [...]
class VisionNode(object):
# [...]
    def callback(color_image, depth_image, camera_info):
        cv_bridge = CvBridge()
        img_cv = cv_bridge.imgmsg_to_cv2(color_image, 'rgba8')
        detections = net.Detect(img_cv, width, height)
```

`img_cv` looks like this:

```python
array([[[ 37,  45,  34, 255],
        [ 40,  48,  37, 255],
        [ 46,  53,  45, 255],
        ...,
        [145, 140, 148, 255],
        [135, 130, 138, 255],
        [122, 117, 125, 255]],

       [[ 37,  45,  34, 255],
        [ 39,  47,  36, 255],
        [ 44,  49,  39, 255],
        ...,
        [141, 137, 142, 255],
        [128, 123, 131, 255],
        [115, 110, 118, 255]],

       [[ 35,  40,  30, 255],
        [ 42,  47,  37, 255],
        [ 45,  50,  40, 255],
        ...,
        [137, 131, 137, 255],
        [129, 124, 132, 255],
        [108, 103, 111, 255]],

       ...,

       [[125, 135, 142, 255],
        [121, 131, 138, 255],
        [124, 131, 137, 255],
        ...,
        [ 42,  49,  53, 255],
        [ 42,  49,  53, 255],
        [ 40,  47,  51, 255]],

       [[121, 126, 135, 255],
        [124, 129, 138, 255],
        [125, 130, 137, 255],
        ...,
        [ 42,  49,  53, 255],
        [ 43,  50,  54, 255],
        [ 42,  49,  53, 255]],

       [[122, 124, 134, 255],
        [127, 129, 139, 255],
        [129, 128, 137, 255],
        ...,
        [ 40,  48,  49, 255],
        [ 42,  50,  51, 255],
        [ 40,  48,  49, 255]]], dtype=uint8)
```

... and its type is `numpy.ndarray`. If it doesn't work, perhaps try other encodings by replacing `'rgba8'` with `'32FC3'` or any other encoding from [image_encodings.h](https://github.com/ros/common_msgs/blob/noetic-devel/sensor_msgs/include/sensor_msgs/image_encodings.h).

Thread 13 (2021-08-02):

can you give a demo of navigaion wihout /Map data , move_base not working for a fixed odom frame

BADAL244, 2021-08-02:
i have setup an robot with max and min velocity and collecting odom data to perform navigation ,please provide a video demo

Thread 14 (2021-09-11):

Robot in Rviz doesnt move straight correctly

Astrobubu, 2021-09-11:
i have played around and converted the wheel calculation to the new odrive standards, using this equation Turns = Counts/EncoderCpr

everything works perfectly except the odometry messages not sending the correct orientation of the robot. more like it is oscillating right and left while moving forward.
here is a link of the movement: https://youtu.be/_V9KNEuVXbw
and the low refresh rate is also a problem :(
do keep in mind the robot is connected to the pc and the data of the movement is coming from odom

the only different thing I'm using is Teensy 4.0

I'm using the First upload of the
here is the Arduino code:

<code>

  #include <ODriveArduino.h>

  //ODrive Objects
  ODriveArduino odrive1(Serial1);

  //ROS
  #include "ros.h"
  #include "geometry_msgs/Twist.h"
  #include <ros/time.h>
  #include <tf/tf.h>
  #include <tf/transform_broadcaster.h>
  #include <nav_msgs/Odometry.h>
  #include <geometry_msgs/Vector3.h>

  ros::NodeHandle nh;
  geometry_msgs::TransformStamped t;
  nav_msgs::Odometry odom_msg;
  ros::Publisher odom_pub("odom", &odom_msg);
  tf::TransformBroadcaster broadcaster;

  // tf variables to be broadcast
  double x = 0;
  double y = 0;
  double theta = 0;

  char base_link[] = "/base_link";
  char odom[] = "/odom";

  // cmd_vel variables to be received to drive with
  float demandx;
  float demandz;

  // timers for the sub-main loop
  unsigned long currentMillis;
  long previousMillis = 0;    // set up timers
  float loopTime = 10;

  // ODrive init stuff
  int button;
  int requested_state;

  // output variables to drive the ODrive
  int forward0;
  int forward1;
  int turn0;
  int turn1;

  // position and velocity variables read from the ODrive
  int vel0;
  int vel1;
  long pos0;
  long pos1;

  // variables to work out the different on each cycle

  long pos0_old;
  long pos1_old;
  long pos0_diff;
  long pos1_diff;
  float pos0_mm_diff;
  float pos1_mm_diff;
  float pos_average_mm_diff;
  float pos_total_mm;

  // ** ROS callback & subscriber **

  void velCallback(  const geometry_msgs::Twist& vel)
  {
       demandx = vel.linear.x;
       demandz = vel.angular.z;
  }

  ros::Subscriber<geometry_msgs::Twist> sub("cmd_vel" , velCallback);            

  // ** Setup **

  void setup() {

    nh.getHardware()->setBaud(115200);      // set baud rate to 115200
    nh.initNode();              // init ROS
    nh.subscribe(sub);          // subscribe to cmd_vel
    nh.advertise(odom_pub);
    broadcaster.init(nh);       // set up broadcaster

    pinMode(2, INPUT_PULLUP);   // ODrive init switch

    Serial1.begin(115200);    // ODrive
    Serial6.begin(115200);    // debug port using a USB-serial adapter (Serial-zero is in use by ros_serial

  }

  // ** Main loop **

  void loop() {

    nh.spinOnce();        // make sure we listen for ROS messages and activate the callback if there is one

    currentMillis = millis();
          if (currentMillis - previousMillis >= loopTime) {  // run a loop every 10ms  
              previousMillis = currentMillis;          // reset the clock to time it

              button = digitalRead(2);                 // init ODrive
              if (button == 0) {
                OdriveInit1();
              }

              float modifier_lin = 1.03;        // scaling factor because the wheels are squashy / there is wheel slip etc.
              float modifier_ang = 1.5;        // scaling factor because the wheels are squashy / there is wheel slip etc.

              forward0 = demandx * ((83466/8192) * modifier_lin) ; // convert m/s into counts/s
              forward1 = demandx * ((83466/8192) * modifier_lin); // convert m/s into counts/s

              turn0 = demandz * ((15091/8192) * modifier_ang);    // convert rads/s into counts/s
              turn1 = demandz * ((15091/8192) * modifier_ang);    // convert rads/s into counts/s

              forward1 = forward1*-1;      // one motor and encoder is mounted facing the other way

              odrive1.SetVelocity(0, forward0 + turn0);
              odrive1.SetVelocity(1, forward1 + turn1);

              // get positions and velocities from ODrive

              pos0 = (odrive1.GetPosition(1)) *-1;           
              pos1 = odrive1.GetPosition(0);

              // work out the difference on each loop, and bookmark the old value
              pos0_diff = pos0 - pos0_old;
              pos1_diff = pos1 - pos1_old;    
              pos0_old = pos0;
              pos1_old = pos1;

              // calc mm from encoder counts
              pos0_mm_diff = pos0_diff / 83.44*8192;
              pos1_mm_diff = pos1_diff / 83.44*8192;

              // calc distance travelled based on average of both wheels
              pos_average_mm_diff = (pos0_mm_diff + pos1_mm_diff) / 2;   // difference in each cycle
              pos_total_mm += pos_average_mm_diff;                       // calc total running total distance

              // calc angle or rotation to broadcast with tf
              float phi = ((pos1_mm_diff - pos0_mm_diff) / 360);

              theta += phi;
    
              if (theta >= TWO_PI) {
                  theta -= TWO_PI;
              }
              if (theta <= (-TWO_PI)) {
                  theta += TWO_PI;
              }

              // calc x and y to broadcast with tf

              y += pos_average_mm_diff * sin(theta);
              x += pos_average_mm_diff * cos(theta);

              // *** broadcast odom->base_link transform with tf ***

              geometry_msgs::TransformStamped t;
                
              t.header.frame_id = odom;
              t.child_frame_id = base_link;
      
              t.transform.translation.x = x/1000;   // convert to metres
              t.transform.translation.y = y/1000;
              t.transform.translation.z = 0;
      
              t.transform.rotation = tf::createQuaternionFromYaw(theta);
              t.header.stamp = nh.now();
                 
              broadcaster.sendTransform(t);

              // *** broadcast odom message ***

              nav_msgs::Odometry odom_msg;
              odom_msg.header.stamp = nh.now();
              odom_msg.header.frame_id = odom;
              odom_msg.pose.pose.position.x = x/1000;
              odom_msg.pose.pose.position.y = y/1000;
              odom_msg.pose.pose.position.z = 0.0;
              odom_msg.pose.pose.orientation = tf::createQuaternionFromYaw(theta);

              odom_msg.child_frame_id = base_link;
              odom_msg.twist.twist.linear.x = ((pos0_mm_diff + pos1_mm_diff) / 2)/10;          // forward linear velovity
              odom_msg.twist.twist.linear.y = 0.0;                                        // robot does not move sideways
              odom_msg.twist.twist.angular.z = ((pos1_mm_diff - pos0_mm_diff) / 360)*100;      // anglular velocity

              odom_pub.publish(&odom_msg);

          } // end of 10ms loop

  } // end of main loop

</code>.

Astrobubu, 2021-09-14:
alright, the new odrive update ruins the entire robot code...

Master Bruton, Don't update ODrive :P

as for the solution, use windows to reflash odrive firmware. ubuntu just throws unicode errors
make sure to follow the instructions and use the STM32Cube tool to reflash, it will do it in a second compared to the crappy dfu tool which will make ur night hell.

Closed 2021-09-14.

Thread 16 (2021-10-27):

How to attach tires to wheel?

kssummer, 2021-10-27:
Does anyone have any tips on how to attach the TPU tires to the wheel? I can't tell if the tolerance is off, or if I'm just weak, but I cannot get the tires around the wheel.

kssummer, 2021-11-02:
Thanks. I ended up putting the tires in hot water and chilling the hub in the freezer. The tire got soft enough to pull over the hub.

Closed 2021-11-02.

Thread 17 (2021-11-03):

Question - faisability and estimated replication time

thibnoel, 2021-11-03:
Hello,

I'm currently pursuing a PhD in robotics, specifically about autonomous exploration and reconstruction of an unknown environment. We are currently using another platform for the project but it is not so reliable mechanically, and seeing the design of the RUR, it seems like it would be a great alternative for us, especially given we use very similar sensors (same LiDAR and a Kinect for RGBD vision). We would probably use an arm-less version since we don't plan any manipulation tasks yet.

I am currently discussing with my supervisors the possibility to try and replicate the RUR during my PhD but it is a bit difficult for me to estimate the time it would take for a team of 1-3 people to rebuild it; we have pretty good knowledge in the team about 3D printing and mechanical assembly so this should not be an issue, it's more on the electronics side that I'm not so sure about the difficulty of such an assembly. This leads me to the following questions :
- how long do you think it would approximately take to wire, test and integrate the wheeled-base electronics with the mechanical assembly for a team of 1-3 people with a beginner/intermediate level in electronics ?
- do you see any steps in the building process that we would need to pay special attention to ?
- if we end up rebuilding and using the RUR for a research project, how would you prefer to be credited (YouTube channel, website, you directly) ?

Thanks in advance for any feedback about this and for the great inspiration your work is in general !
Thibault

XRobots, 2021-11-03:
It took me about 2 weeks on my own to build it all and get the base up and running and navigating (the first two videos in the playlist). I do have a lot of printers though so I could make all the parts concurrently. I was still learning about ROS at the same time and this is the first ROS robot I build that worked properly.

https://www.youtube.com/playlist?list=PLpwJoq86vov_wIh6f-A1ZkjCwo11jkbe3

One issue now is that ODrive have updated their firmware and Arduino Library, so all the units are now different (turns instead of encoder counts), so you'll have to work through converting the units if you buy a new ODrive.

Feel free to credit my YouTube if you wish, although the whole thing is open source, so just publishing any modified source would be fine.

thibnoel, 2021-11-03:
Thanks a lot for your answer ! Do you know if anyone has attempted/succeeded to replicate the project yet ?
I guess the new ODrive firmware should not be too much of an issue if it's only a matter of unit conversions

XRobots, 2021-11-03:
I'm not aware of anyone who's completed it. A few others have asked question - I believe there are some closed issues.

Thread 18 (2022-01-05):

Timed out waiting for transform from base_link to map to become available before running costmap, tf error: canTransform: target_frame map does not exist.. canTransform returned after 0.100065 timeout was 0.1

MiPlayer123, 2022-01-05:
Hello

I am running into issues when running `roslaunch rur_navigation rur_navigation.launch` with `roslaunch rur rur_bringup.launch`.
This is the error:
```
process[map_server-1]: started with pid [27581]
process[amcl-2]: started with pid [27582]
process[move_base-3]: started with pid [27583]
process[rviz-4]: started with pid [27596]
[ WARN] [1641341048.747458020]: Request for map failed; trying again...
[ WARN] [1641341053.709191464]: Timed out waiting for transform from base_link to map to become available before running costmap, tf error: canTransform: target_frame map does not exist.. canTransform returned after 0.100065 timeout was 0.1.
[ WARN] [1641341058.731377300]: Timed out waiting for transform from base_link to map to become available before running costmap, tf error: canTransform: target_frame map does not exist.. canTransform returned after 0.1003 timeout was 0.1.
[ WARN] [1641341063.771360315]: Timed out waiting for transform from base_link to map to become available before running costmap, tf error: canTransform: target_frame map does not exist.. canTransform returned after 0.100305 timeout was 0.1.
[ WARN] [1641341065.510832061]: No laser scan received (and thus no pose updates have been published) for 1641341065.510745 seconds.  Verify that data is being published on the /scan topic.
[ WARN] [1641341068.811848131]: Timed out waiting for transform from base_link to map to become available before running costmap, tf error: canTransform: target_frame map does not exist.. canTransform returned after 0.100372 timeout was 0.1.
```

I am not sure where the error is coming from. Thanks in advance.

XRobots, 2022-01-05:
Looks like the map is missing as well as the laser data. Can you actually see the laser data getting published on /scan in RVIZ and does it sync up with TF?

Have you actually created the map yet?

MiPlayer123, 2022-01-06:
For now, I was just using the default map, which is set as `house_map` in the navigation launch file `<arg name="map_file" default="$(find rur_navigation)/maps/house_map.yaml"/>`. I am not sure why the error exists as the map and pgm file exist.

I use `rur_bringup.launch`, which has the laser scan included `<include file="$(find rplidar_ros)/launch/rplidar.launch" />`, but I don't see any data being published in RVIZ. When I run the rplidar node separately, I am able to see the data being published.

3087575358, 2023-06-07:
I got the same question, which shows that the status of laserscan and others are error,have you get done with that yet?
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

3087575358, 2023-06-07:
I got the same question, which shows that the status of laserscan and others are error,have you got done with that yet?
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

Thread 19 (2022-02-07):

Robot vibrating

LinusNEP, 2022-02-07:
Hello,
The simulation worked fine for me, although the robot always gets stuck on a narrow passage during autonomous navigation. However, I am trying to implement this on the real robot but no luck at the moment.
I have an ODrive controller 56v v3.6, Arduino mega and jetson nano but a different wheel (hoverboard 165.1 mm wheel diameter).
When I run the Arduino ROS serial node, the wheel spins but with heavy vibration. I anticipate it could be errors due to the encoder and wheel parameters calculation. Also, the robot moves quite slow in RViz (sometimes unnoticeable) compared to real-time.
I am wondering if you could spare some time to assist me to fix it.

XRobots, 2022-02-08:
ODrive updated their firmware to use 'turns', which is a motor revolution, instead of encoder counts. So you'll probably need to adjust all the units because they are 8192 times too big now.

LinusNEP, 2022-02-08:
@XRobots Thanks for you reply. So in this case,  I have to divide the previous  values by 90 cpr to get it in turns/m, turns/s and rad/s (the values written in red). I am wondering if that is right?
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

XRobots, 2022-02-09:
It looks like the right process, but I haven't checked the maths ;-)

LinusNEP, 2022-02-09:
Ok, thank you very much for your concern. I would be pleased if you could find out time to go through it. I tested the new values with the robot and it seems to work fine at low speed. However, there are still vibration driving the robot at high speed.

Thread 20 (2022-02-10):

GR-WM2 replacement?

kssummer, 2022-02-10:
Is it possible to source the GR-WM2 somewhere? Or is there a suitable replacement?

Looks like the carriage motor has been discontinued: https://gimsonrobotics.co.uk/categories/dc-electric-motors/products/gr-wm2-24v-dc-rs-595-motor-with-152-1-gearbox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

They have a replacement, but it has some issues:
(a) the motor (gearbox) mounting holes are only on one side, which might not allow for enough support from the 3D printed mounts
(b) I expect the shaft won't be lined up the same as the GR-WM2. The belt needs to be driven vertically to move the carriage, which means we'd have to redesign the CAD to line up the motor, idler, and carriage.

Issue (a) isn't that big of a deal, I could fab a piece of aluminum/steel to securely mount the motor, but issue (b) is a big deal for me. It requires some CAD redesign I don't have the chops for. Also, I expect any replacement will have this same issue unless the shaft offset is exactly the same.

XRobots, 2022-02-11:
I bought a bunch of those motors when I built Performance Robots so I've not really investigated a replacement I'm afraid. I guess it'll take some redesign to incorporate a totally different motor.

kssummer, 2022-02-11:
Hi James,

Any chance you'd be willing to sell me one of those motors?

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

XRobots, 2022-02-11:
Sorry I don't have enough spare - there are eight on robots at the moment and I have two extras which I use when I need powerful differential drive in a project, but they are also the two spares for Performance Robots if I take them to events again.

kssummer, 2022-02-11:
No worries. Thanks for the response and thanks for all your work on these
cool robot projects

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

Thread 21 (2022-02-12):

CAD for utility stick belt pulley

kssummer, 2022-02-12:
Do you have the CAD model, or STL, for the utility stick belt pulley? At first, I thought it would be the same as the O-Drive pulley, but it seems to have a thicker belt, and a larger pulley.

FYI, I'll probably have to find a 3D model for a similar pulley because the replacement motors I'm finding for the GR-WM2 all have 8mm shafts on them. Can you tell me me the belt size (pitch, width, and length)?

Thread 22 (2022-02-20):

Wiring diagram?

kssummer, 2022-02-20:
Is there a wiring diagram for this robot?
I'm trying to understand how the relay, switches, voltmeters, and control boards are connected.

XRobots, 2022-02-20:
There isn't a wiring diagram, but the details are here: https://youtu.be/dEPvZZ4luV4?list=PLpwJoq86vov_wIh6f-A1ZkjCwo11jkbe3&t=202

The switches turn on power from the two batteries, the 12V one is for the Xavier and the 24V one is for the ODrive. The meters are wired after the switches so they only come on when the power is on. The relay is used to switch on the power to the ODrive because the 10A toggle isn't enough to switch 20A per axis.

filoucool, 2022-04-14:
Hi! I also had a question about the wiring between the Odrive and the Teensy... To what Pins on the Odrive and teensy do the white and yellow cables go to? I think I figured out that it goes to the teensy's Serial1 pins but I cant figure out for the Odrive...
Thanks!

XRobots, 2022-04-14:
You need to look at the ODrive documentation so your wiring matches the current firmware: https://docs.odriverobotics.com/v/latest/pinout.html

Closed 2022-04-14.

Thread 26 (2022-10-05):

Navigation failure

kssummer, 2022-10-05:
I'm having trouble with the navigation stack. When I make a waypoint, my robot starts jerking around; no smooth movement. Today the robot fell over because of this. Any idea on what could cause this? Or how to fix it?

For background, I was able to get the robot moving smoothly. I had to change the arduino code to convert the Odrive turns to millimeters, but now its fine. The odom, base_link, and lazer show up in rviz. I can drive around fine, the lazer scan stays put, and I have built a map of my living room. I launched the navigation stack, the map comes up, although the costmap looks rather inflated, but the robot is oriented right, assuming I place it in my room where I started the map.

It looks like the navigation stack is continuously updating its plan. The robot never really gets a chance to drive straight; instdead it whips back and forth like a low-rent murder bot. My dogs are concerned.

(I rolled back the git repository to the original navigation commit, before the simulation stuff was merged just to be sure that wasnt the issue, but both versions have this issue. In the latest code, the lazer scan gets out of synch with the map; that doesn't happen in the original version)

Here's the log from the navigation:
roslaunch rur_navigation rur_navigation.launch map_file:=$HOME/ros_catkin_ws/src/rur_navigation/maps/livingroom_sean.yaml
... logging to /home/sean/.ros/log/546ce954-4473-11ed-920f-bfb2a73f92b8/roslaunch-beefcake-62996.log
Checking log directory for disk usage. This may take a while.
Press Ctrl-C to interrupt
Done checking log file disk usage. Usage is <1GB.

started roslaunch server http://beefcake:38965/

SUMMARY
========

PARAMETERS
 * /amcl/base_frame_id: base_link
 * /amcl/gui_publish_rate: 50.0
 * /amcl/initial_pose_a: 0.0
 * /amcl/initial_pose_x: 0.0
 * /amcl/initial_pose_y: 0.0
 * /amcl/kld_err: 0.02
 * /amcl/laser_lambda_short: 0.1
 * /amcl/laser_likelihood_max_dist: 2.0
 * /amcl/laser_max_beams: 180
 * /amcl/laser_max_range: 3.5
 * /amcl/laser_model_type: likelihood_field
 * /amcl/laser_sigma_hit: 0.2
 * /amcl/laser_z_hit: 0.5
 * /amcl/laser_z_max: 0.05
 * /amcl/laser_z_rand: 0.5
 * /amcl/laser_z_short: 0.05
 * /amcl/max_particles: 3000
 * /amcl/min_particles: 500
 * /amcl/odom_alpha1: 0.1
 * /amcl/odom_alpha2: 0.1
 * /amcl/odom_alpha3: 0.1
 * /amcl/odom_alpha4: 0.1
 * /amcl/odom_frame_id: odom
 * /amcl/odom_model_type: diff
 * /amcl/recovery_alpha_fast: 0.0
 * /amcl/recovery_alpha_slow: 0.0
 * /amcl/resample_interval: 1
 * /amcl/transform_tolerance: 0.5
 * /amcl/update_min_a: 0.2
 * /amcl/update_min_d: 0.2
 * /move_base/DWAPlannerROS/acc_lim_theta: 3.2
 * /move_base/DWAPlannerROS/acc_lim_x: 2.5
 * /move_base/DWAPlannerROS/acc_lim_y: 0.0
 * /move_base/DWAPlannerROS/controller_frequency: 10.0
 * /move_base/DWAPlannerROS/forward_point_distance: 0.325
 * /move_base/DWAPlannerROS/goal_distance_bias: 20.0
 * /move_base/DWAPlannerROS/latch_xy_goal_tolerance: False
 * /move_base/DWAPlannerROS/max_scaling_factor: 0.2
 * /move_base/DWAPlannerROS/max_vel_theta: 2.75
 * /move_base/DWAPlannerROS/max_vel_trans: 0.22
 * /move_base/DWAPlannerROS/max_vel_x: 0.22
 * /move_base/DWAPlannerROS/max_vel_y: 0.0
 * /move_base/DWAPlannerROS/min_vel_theta: 1.37
 * /move_base/DWAPlannerROS/min_vel_trans: 0.11
 * /move_base/DWAPlannerROS/min_vel_x: -0.22
 * /move_base/DWAPlannerROS/min_vel_y: 0.0
 * /move_base/DWAPlannerROS/occdist_scale: 0.02
 * /move_base/DWAPlannerROS/oscillation_reset_dist: 0.05
 * /move_base/DWAPlannerROS/path_distance_bias: 32.0
 * /move_base/DWAPlannerROS/publish_cost_grid_pc: True
 * /move_base/DWAPlannerROS/publish_traj_pc: True
 * /move_base/DWAPlannerROS/scaling_speed: 0.25
 * /move_base/DWAPlannerROS/sim_time: 1.5
 * /move_base/DWAPlannerROS/stop_time_buffer: 0.2
 * /move_base/DWAPlannerROS/vth_samples: 40
 * /move_base/DWAPlannerROS/vx_samples: 20
 * /move_base/DWAPlannerROS/vy_samples: 0
 * /move_base/DWAPlannerROS/xy_goal_tolerance: 0.05
 * /move_base/DWAPlannerROS/yaw_goal_tolerance: 0.17
 * /move_base/base_local_planner: dwa_local_planner...
 * /move_base/conservative_reset_dist: 3.0
 * /move_base/controller_frequency: 10.0
 * /move_base/controller_patience: 15.0
 * /move_base/global_costmap/global_frame: map
 * /move_base/global_costmap/inflation_layer/cost_scaling_factor: 5.0
 * /move_base/global_costmap/inflation_layer/enabled: True
 * /move_base/global_costmap/inflation_layer/inflation_radius: 0.3
 * /move_base/global_costmap/map_type: costmap
 * /move_base/global_costmap/obstacle_layer/combination_method: 1
 * /move_base/global_costmap/obstacle_layer/enabled: True
 * /move_base/global_costmap/obstacle_layer/inflation_radius: 0.2
 * /move_base/global_costmap/obstacle_layer/laser_scan_sensor/clearing: True
 * /move_base/global_costmap/obstacle_layer/laser_scan_sensor/data_type: LaserScan
 * /move_base/global_costmap/obstacle_layer/laser_scan_sensor/marking: True
 * /move_base/global_costmap/obstacle_layer/laser_scan_sensor/topic: scan
 * /move_base/global_costmap/obstacle_layer/observation_sources: laser_scan_sensor
 * /move_base/global_costmap/obstacle_layer/obstacle_range: 2.5
 * /move_base/global_costmap/obstacle_layer/raytrace_range: 3.5
 * /move_base/global_costmap/obstacle_layer/track_unknown_space: False
 * /move_base/global_costmap/plugins: [{'name': 'static...
 * /move_base/global_costmap/publish_frequency: 5.0
 * /move_base/global_costmap/robot_base_frame: base_link
 * /move_base/global_costmap/robot_radius: 0.225
 * /move_base/global_costmap/static_layer/enabled: True
 * /move_base/global_costmap/static_layer/map_topic: map
 * /move_base/global_costmap/static_map: True
 * /move_base/global_costmap/transform_tolerance: 1.0
 * /move_base/global_costmap/update_frequency: 5.0
 * /move_base/local_costmap/global_frame: map
 * /move_base/local_costmap/height: 5
 * /move_base/local_costmap/inflation_layer/cost_scaling_factor: 5.0
 * /move_base/local_costmap/inflation_layer/enabled: True
 * /move_base/local_costmap/inflation_layer/inflation_radius: 0.3
 * /move_base/local_costmap/map_type: costmap
 * /move_base/local_costmap/obstacle_layer/combination_method: 1
 * /move_base/local_costmap/obstacle_layer/enabled: True
 * /move_base/local_costmap/obstacle_layer/inflation_radius: 0.2
 * /move_base/local_costmap/obstacle_layer/laser_scan_sensor/clearing: True
 * /move_base/local_costmap/obstacle_layer/laser_scan_sensor/data_type: LaserScan
 * /move_base/local_costmap/obstacle_layer/laser_scan_sensor/marking: True
 * /move_base/local_costmap/obstacle_layer/laser_scan_sensor/topic: scan
 * /move_base/local_costmap/obstacle_layer/observation_sources: laser_scan_sensor
 * /move_base/local_costmap/obstacle_layer/obstacle_range: 2.5
 * /move_base/local_costmap/obstacle_layer/raytrace_range: 3.5
 * /move_base/local_costmap/obstacle_layer/track_unknown_space: False
 * /move_base/local_costmap/plugins: [{'name': 'static...
 * /move_base/local_costmap/publish_frequency: 1.0
 * /move_base/local_costmap/resolution: 0.1
 * /move_base/local_costmap/robot_base_frame: base_link
 * /move_base/local_costmap/robot_radius: 0.225
 * /move_base/local_costmap/rolling_window: True
 * /move_base/local_costmap/static_layer/enabled: True
 * /move_base/local_costmap/static_layer/map_topic: map
 * /move_base/local_costmap/static_map: False
 * /move_base/local_costmap/transform_tolerance: 0.5
 * /move_base/local_costmap/update_frequency: 2.0
 * /move_base/local_costmap/width: 5
 * /move_base/oscillation_distance: 0.2
 * /move_base/oscillation_timeout: 10.0
 * /move_base/planner_frequency: 5.0
 * /move_base/planner_patience: 5.0
 * /move_base/shutdown_costmaps: False
 * /rosdistro: noetic
 * /rosversion: 1.15.14

NODES
  /
    amcl (amcl/amcl)
    map_server (map_server/map_server)
    move_base (move_base/move_base)
    rviz (rviz/rviz)

ROS_MASTER_URI=http://beefcake:11311/
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
XRobots, 2022-10-05:
Hello, I don't know what to do with this, I haven't looked at the robot for years.

ODrive updated their firmware so the units are different. I have no easy way to test your pull request before merging it. Feel free to fork the repository / publish your own version though.

kssummer, 2022-10-05:
@PranshuTople maybe you can help point me in the right direction here? I updated the arduino code to convert the new units from the new ODrive firmware. I can drive the robot around with the rosremote and create a good map, but whenever I make a way point with the navigation stack, the robot stutters its movement. Any ideas on what I can look at?

PranshuTople, 2022-11-17:
Hey @kssummer,

Can you share a video of your robot's motion first in teleoperation mode and later in navigation? I want to see how it behaves in order to comment on anything

FrancisTembo, 2023-07-23:
Couldn't get the unit conversion right. @kssummer would you mind sharing your fix?

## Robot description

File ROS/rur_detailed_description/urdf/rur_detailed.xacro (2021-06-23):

<?xml version="1.0" ?>
<robot name="rur_detailed" xmlns:xacro="http://www.ros.org/wiki/xacro">

<xacro:include filename="$(find rur_detailed_description)/urdf/materials.xacro" />
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

<xacro:include filename="$(find rur_detailed_description)/gazebo/rur_detailed_materials.gazebo" />
<xacro:include filename="$(find rur_detailed_description)/gazebo/rur_detailed_physics.gazebo" />
<xacro:include filename="$(find rur_detailed_description)/gazebo/rur_detailed_plugins.gazebo" />

<link name="base_link">
  <inertial>
    <origin rpy="0 0 0" xyz="0.008717050480319273 0.0013081620436010979 0.15115173825671988"/>
    <mass value="15.428530536945836"/>
    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
  </inertial>
  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
</link>

<link name="right_wheel">
  <inertial>
    <origin rpy="0 0 0" xyz="-1.828063402709465e-05 0.05312247246161367 0.0002521115303902449"/>
    <mass value="9.856921104469992"/>
    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
  </inertial>
  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
</link>

<link name="left_wheel">
  <inertial>
    <origin rpy="0 0 0" xyz="-1.8254554994090065e-05 -0.0531169103077688 0.0002522130405125389"/>
    <mass value="9.871217353742987"/>
    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
  </inertial>
  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
</link>

<link name="right_tyre">
  <inertial>
    <origin rpy="0 0 0" xyz="-5.919068486634321e-08 0.011578960710706687 0.00016105311301901903"/>
    <mass value="4.766678644162142"/>
    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
  </inertial>
  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
</link>

<link name="left_tyre">
  <inertial>
    <origin rpy="0 0 0" xyz="9.30327782468428e-09 -0.011578963887744514 0.000161051324790773"/>
    <mass value="4.766678875971219"/>
    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
  </inertial>
  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
</link>

<link name="front_caster">
  <inertial>
    <origin rpy="0 0 0" xyz="-0.025000797505036393 -2.9865544783409456e-16 -0.030208086053412367"/>
    <mass value="0.4573656248802168"/>
    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
  </inertial>
  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
</link>

<link name="back_caster">
  <inertial>
    <origin rpy="0 0 0" xyz="0.024999202494963513 -3.2214520215812444e-16 -0.030208086053412374"/>
    <mass value="0.4573656248802169"/>
    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
  </inertial>
  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
</link>

<link name="lid">
  <inertial>
    <origin rpy="0 0 0" xyz="-0.20973058370001274 -0.0002000297507654507 0.021779111268977636"/>
    <mass value="18.187373287828525"/>
    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
  </inertial>
  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
</link>

<link name="lidar">
  <inertial>
    <origin rpy="0 0 0" xyz="-2.3483549826952554e-09 -3.4770506128023716e-07 0.009561590682608923"/>
    <mass value="0.0886181648250366"/>
    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
  </inertial>
  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
</link>

<link name="electronics_lid">
  <inertial>
    <origin rpy="0 0 0" xyz="-0.0511574994774171 -0.011997734212864706 -0.0015000000000000568"/>
    <mass value="0.633989646973267"/>
    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
  </inertial>
  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
</link>

<link name="long_bar">
  <inertial>
    <origin rpy="0 0 0" xyz="0.03584192761999582 0.003225175684225926 0.4595434632519135"/>
    <mass value="7.553317644619513"/>
    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
  </inertial>
  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
</link>

<link name="head">
  <inertial>
    <origin rpy="0 0 0" xyz="-0.07213061988974884 -0.0012048920814073697 0.13382726687589575"/>
    <mass value="23.76468895609019"/>
    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
  </inertial>
  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
</link>

<link name="visor">
  <inertial>
    <origin rpy="0 0 0" xyz="0.02896510148077766 0.0680499999999997 0.031790396670437815"/>
    <mass value="1.3383367623018805"/>
    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
  </inertial>
  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
</link>

<link name="monitor_cover">
  <inertial>
    <origin rpy="0 0 0" xyz="0.025963694079177757 0.06804999764452557 -0.03724939393816329"/>
    <mass value="1.1102091778876433"/>
    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
  </inertial>
  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
</link>

<link name="right_ear">
  <inertial>
    <origin rpy="0 0 0" xyz="0.04558838834048603 -0.006250460774062022 2.75422459194985e-06"/>
    <mass value="0.05021038391016931"/>
    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
  </inertial>
  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
</link>

<link name="left_ear">
  <inertial>
    <origin rpy="0 0 0" xyz="0.04558838821639881 0.006350460758356213 2.7542230829347147e-06"/>
    <mass value="0.050210384315252085"/>
    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
  </inertial>
  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
</link>

<link name="monitor">
  <inertial>
    <origin rpy="0 0 0" xyz="0.010564793341225787 5.000000000079698e-05 -0.037888190449721026"/>
    <mass value="0.09619500000000142"/>
    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
  </inertial>
  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
</link>

<link name="left_antenna">
  <inertial>
    <origin rpy="0 0 0" xyz="-0.06681873348160798 0.027729801813354465 -0.006847664607670945"/>
    <mass value="0.185506067385235"/>
    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
  </inertial>
  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
</link>

<link name="right_antenna">
  <inertial>
    <origin rpy="0 0 0" xyz="-0.06681872625021491 -0.027629817768358322 -0.006847111322377364"/>
    <mass value="0.18550683738354107"/>
    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
  </inertial>
  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
</link>

<link name="camera_link">
  <inertial>
    <origin rpy="0 0 0" xyz="-0.001604468363459316 0.07205272744017827 -0.002548711859325259"/>
    <mass value="0.3739643327489875"/>
    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
  </inertial>
  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
</link>

<link name="realsense">
  <inertial>
    <origin rpy="0 0 0" xyz="0.004830412362641728 5.000000000015024e-05 0.00650000017136354"/>
    <mass value="0.03735280587989202"/>
    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
  </inertial>
  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
</link>

<joint name="motor_right" type="continuous">
  <origin rpy="0 0 0" xyz="0.0 -0.227 0.099839"/>
  <parent link="base_link"/>
  <child link="right_wheel"/>
  <axis xyz="0.0 1.0 0.0"/>
</joint>

<joint name="motor_left" type="continuous">
  <origin rpy="0 0 0" xyz="0.0 0.227 0.099839"/>
  <parent link="base_link"/>
  <child link="left_wheel"/>
  <axis xyz="0.0 1.0 0.0"/>
</joint>

<joint name="Rigid3" type="fixed">
  <origin rpy="0 0 0" xyz="0.0 0.027 0.000161"/>
  <parent link="right_wheel"/>
  <child link="right_tyre"/>
</joint>

<joint name="Rigid4" type="fixed">
  <origin rpy="0 0 0" xyz="0.0 -0.027 0.000161"/>
  <parent link="left_wheel"/>
  <child link="left_tyre"/>
</joint>

<joint name="Rigid5" type="fixed">
  <origin rpy="0 0 0" xyz="0.172 0.0 0.07"/>
  <parent link="base_link"/>
  <child link="front_caster"/>
</joint>

<joint name="Rigid6" type="fixed">
  <origin rpy="0 0 0" xyz="-0.172 0.0 0.07"/>
  <parent link="base_link"/>
  <child link="back_caster"/>
</joint>

<joint name="Rigid7" type="fixed">
  <origin rpy="0 0 0" xyz="0.225 0.0002 0.25"/>
  <parent link="base_link"/>
  <child link="lid"/>
</joint>

<joint name="Rigid8" type="fixed">
  <origin rpy="0 0 0" xyz="-0.0675 -0.0002 0.05"/>
  <parent link="lid"/>
  <child link="lidar"/>
</joint>

<joint name="Rigid9" type="fixed">
  <origin rpy="0 0 0" xyz="-0.26 0.0148 0.03"/>
  <parent link="lid"/>
  <child link="electronics_lid"/>
</joint>

<joint name="Rigid10" type="fixed">
  <origin rpy="0 0 0" xyz="-0.21 -0.0002 0.041"/>
  <parent link="lid"/>
  <child link="long_bar"/>
</joint>

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

<joint name="slider" type="fixed">
  <origin rpy="0 0 0" xyz="0.096 0.0 0.714"/>
  <parent link="long_bar"/>
  <child link="head"/>
</joint>

<joint name="Rigid12" type="fixed">
  <origin rpy="0 0 0" xyz="0.0283 -0.068 0.124264"/>
  <parent link="head"/>
  <child link="visor"/>
</joint>

<joint name="Rigid13" type="fixed">
  <origin rpy="0 0 0" xyz="0.033358 0.0 0.081794"/>
  <parent link="visor"/>
  <child link="monitor_cover"/>
</joint>

<joint name="Rigid14" type="fixed">
  <origin rpy="0 0 0" xyz="-0.13125 -0.134173 0.175"/>
  <parent link="head"/>
  <child link="right_ear"/>
</joint>

<joint name="Rigid15" type="fixed">
  <origin rpy="0 0 0" xyz="-0.13125 0.134173 0.175"/>
  <parent link="head"/>
  <child link="left_ear"/>
</joint>

<joint name="Rigid16" type="fixed">
  <origin rpy="0 0 0" xyz="0.011373 0.068 0.020695"/>
  <parent link="monitor_cover"/>
  <child link="monitor"/>
</joint>

<joint name="Rigid17" type="fixed">
  <origin rpy="0 0 0" xyz="0.07175 0.076 0.33"/>
  <parent link="head"/>
  <child link="left_antenna"/>
</joint>

<joint name="Rigid18" type="fixed">
  <origin rpy="0 0 0" xyz="0.07175 -0.076 0.33"/>
  <parent link="head"/>
  <child link="right_antenna"/>
</joint>

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

<joint name="camera_joint" type="fixed">
  <origin rpy="0 0 0" xyz="0.07175 -0.072 0.33"/>
  <parent link="head"/>
  <child link="camera_link"/>
</joint>

<joint name="Rigid20" type="fixed">
  <origin rpy="0 0 0" xyz="0.030692 0.072 -0.0075"/>
  <parent link="camera_link"/>
  <child link="realsense"/>
</joint>

</robot>

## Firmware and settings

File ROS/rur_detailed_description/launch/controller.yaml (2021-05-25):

rur_detailed_controller:
  # Publish all joint states -----------------------------------
  joint_state_controller:
    type: joint_state_controller/JointStateController
    publish_rate: 50

  # Position Controllers --------------------------------------
  motor_right_position_controller:
    type: effort_controllers/JointPositionController
    joint: motor_right
    pid: {p: 100.0, i: 0.01, d: 10.0}
  motor_left_position_controller:
    type: effort_controllers/JointPositionController
    joint: motor_left
    pid: {p: 100.0, i: 0.01, d: 10.0}
  slider_position_controller:
    type: effort_controllers/JointPositionController
    joint: slider
    pid: {p: 100.0, i: 0.01, d: 10.0}
  camera_joint_position_controller:
    type: effort_controllers/JointPositionController
    joint: camera_joint
    pid: {p: 100.0, i: 0.01, d: 10.0}

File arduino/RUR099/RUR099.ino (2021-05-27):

#include <Dynamixel2Arduino.h>

#define DXL_SERIAL Serial2

//ODrive
#include <ODriveArduino.h>

//ODrive Objects
ODriveArduino odrive1(Serial1);

//ROS
#include "ros.h"
#include "geometry_msgs/Twist.h"
#include <ros/time.h>
#include <tf/tf.h>
#include <tf/transform_broadcaster.h>
#include <nav_msgs/Odometry.h>
#include <geometry_msgs/Vector3.h>
#include <std_msgs/UInt16.h>

ros::NodeHandle nh;
geometry_msgs::TransformStamped t;
nav_msgs::Odometry odom_msg;
ros::Publisher odom_pub("odom", &odom_msg);
tf::TransformBroadcaster broadcaster;

std_msgs::UInt16 eye_msg;
ros::Publisher pub_eye("eye", &eye_msg);

// tf variables to be broadcast
double x = 0;
double y = 0;
double theta = 0;

float xArm;
float yArm;
float zArm;

char arm[] = "/arm";
char base_link[] = "/base_link";
char odom[] = "/odom";

// cmd_vel variables to be received to drive with
float demandx;
float demandz;

float demandArmX;           // demand values from sticks
float demandArmY;
float demandArmZ;  

float demandEye;        

float demandArmZAccum;      // accumulators for manual mode
float demandArmXAccum;
float demandArmYAccum;
float demandArmXAccum2;
float demandArmYAccum2;

float demandEyeAccum;
float demandEyeAccum2;

// timers for the sub-main loop
unsigned long currentMillis;
long previousMillis = 0;    // set up timers
float loopTime = 10;

// ODrive init stuff
int button1;
int button2;
int prox;
int requested_state;

int mode;
int modeOld;
int homeFlag = 0;

// output variables to drive the ODrive
int forward0;
int forward1;
int turn0;
int turn1;

// position and velocity variables read from the ODrive
int vel0;
int vel1;
long pos0;
long pos1;

// variables to work out the different on each cycle

long pos0_old;
long pos1_old;
long pos0_diff;
long pos1_diff;
float pos0_mm_diff;
float pos1_mm_diff;
float pos_average_mm_diff;
float pos_total_mm;

// encoder stuff

#define encoder0PinA 18      // encoder 1
#define encoder0PinB 19

volatile long encoder0Pos = 0;    // encoder 1

// arm variables

const uint8_t DXL_DIR_PIN = 21; // DYNAMIXEL Shield DIR PIN 
const float DXL_PROTOCOL_VERSION = 2.0;

int offset10 = 90;   // 90 folded
int offset20 = 180;  // 270 folded
int offset30 = 180;  // 90 folded
int offset40 = 180;  // 180 mid
int offset50 = 180;  // 180 mid

float pos10;
float pos20;
float pos30;
float pos40;
float pos50;
float pos50Pub;

float finPos10;
float finPos20;
float finPos30;
float finPos40;
float finPos50;

float finPos10Prev;
float finPos20Prev;
float finPos30Prev;
float finPos40Prev;
float finPos50Prev;

float armX = 350;         // variables received from Vector3 message to drive arm
float armY = 145;
float armZ = 0;

int pot1;   // test pots from video part 4
int pot2;

long previousFoldMillis = 0;
int fold = 0;
int foldFlag = 0;

// moving the foot forwards or backwards in the side plane
float shoulderAngle2;
float shoulderAngle2a;
float shoulderAngle2Degrees;
float shoulderAngle2aDegrees;
float y3;
float y2;
float x3;
float x2;

// side plane of individual leg only
#define lowerLength 370     
#define upperLength 238
float armLength;
float shoulderAngle1;
float shoulderAngle1Degrees;
float shoulderAngle1a;   
float elbowAngle1;
float elbowAngle1a;
float elbowAngle1Degrees;

Dynamixel2Arduino dxl(DXL_SERIAL, DXL_DIR_PIN);

//This namespace is required to use Control table item names
using namespace ControlTableItem;

// ** ROS callback & subscriber **

void velCallback(  const geometry_msgs::Twist& vel)
{
     demandx = vel.linear.x;
     demandz = vel.angular.z;
          
     demandArmX = vel.angular.x;
     demandArmY = vel.angular.y;
     demandArmZ = vel.linear.z;

     demandEye = vel.linear.y;
}

void foldArm( const std_msgs::UInt16& cmd_msg){
  mode = (cmd_msg.data);
  if (mode != modeOld) {
    if (mode == 1) {
      fold = 1;
    }
    else if (mode == 2) {
      fold = 0;
    }
  }
  modeOld = mode;
}

void armCoords( const geometry_msgs::Vector3 cmd_msg){
  armX = (cmd_msg.x);
  armY = (cmd_msg.y);
  armZ = (cmd_msg.z);
}

ros::Subscriber<geometry_msgs::Twist> sub("cmd_vel" , velCallback);  
ros::Subscriber<std_msgs::UInt16> sub2("buttons", foldArm);
ros::Subscriber<geometry_msgs::Vector3> sub3("armCoords", armCoords);

// ** Setup **

void setup() {

  nh.getHardware()->setBaud(115200);      // set baud rate to 115200
  nh.initNode();              // init ROS
  nh.subscribe(sub);          // subscribe to cmd_vel
  nh.subscribe(sub2);          // subscribe to arm fold
  nh.subscribe(sub3);          // subscribe to Vector3 arm messages
  nh.advertise(odom_pub);
  broadcaster.init(nh);       // set up broadcaster
  nh.advertise(pub_eye);   // advertise eye topic

  pinMode(2, INPUT_PULLUP);   // ODrive init switch
  pinMode(3, INPUT_PULLUP);   // linear axis home switch

  pinMode(encoder0PinA, INPUT_PULLUP);    // encoder pins
  pinMode(encoder0PinB, INPUT_PULLUP);

  pinMode(14, OUTPUT);    // linear motor drive
  pinMode(15, OUTPUT);

  pinMode(41, INPUT_PULLUP);  // proximity switch

  attachInterrupt(18, doEncoderA, CHANGE);
  attachInterrupt(19, doEncoderB, CHANGE);

  Serial1.begin(115200);    // ODrive
  Serial6.begin(115200);    // debug port using a USB-serial adapter (Serial-zero is in use by ros_serial

  // Dynamixel setup

  dxl.begin(57600);
  dxl.setPortProtocolVersion(DXL_PROTOCOL_VERSION);
  dxl.ping(10);
  dxl.ping(20);
  dxl.ping(30);
  dxl.ping(40);
  dxl.ping(50);
  // Turn off torque when configuring items in EEPROM area
  dxl.torqueOff(10);
  dxl.torqueOff(20);
  dxl.torqueOff(30);
  dxl.torqueOff(40);
  dxl.torqueOff(50);
  dxl.setOperatingMode(10, OP_POSITION);
  dxl.setOperatingMode(20, OP_POSITION);
  dxl.setOperatingMode(30, OP_POSITION);
  dxl.setOperatingMode(40, OP_POSITION);
  dxl.torqueOn(10);
  dxl.torqueOn(20);
  dxl.torqueOn(30);
  dxl.torqueOn(40);
  dxl.torqueOn(50);
  // Limit the maximum velocity in Position Control Mode. Use 0 for Max speed
  dxl.writeControlTableItem(PROFILE_VELOCITY, 10, 30);
  dxl.writeControlTableItem(PROFILE_VELOCITY, 20, 30);
  dxl.writeControlTableItem(PROFILE_VELOCITY, 30, 30);
  dxl.writeControlTableItem(PROFILE_VELOCITY, 40, 30);
  dxl.writeControlTableItem(PROFILE_VELOCITY, 50, 30);

  fold = 1;   // start with arm folded out for testing

}

// ** Main loop **

void loop() {

  nh.spinOnce();        // make sure we listen for ROS messages and activate the callback if there is one

  currentMillis = millis();
        if (currentMillis - previousMillis >= loopTime) {  // run a loop every 10ms          
            previousMillis = currentMillis;          // reset the clock to time it

            button1 = digitalRead(2);                 // init ODrive
            if (button1 == 0) {
              OdriveInit1();
            }  

            button2 = digitalRead(3);                 // home linear axis
            prox = digitalRead(41);                   // proximity switch

            //demandArmZAccum = demandArmZAccum + (demandArmZ * 160);   /// add or subtract to the value on each cycle.
            //demandArmZAccum = constrain (demandArmZAccum, -50000,0);
            demandArmZAccum = armZ;   // use data from Vector3 message instead
            demandArmZAccum = constrain (demandArmZAccum, -50000,0);

            if  (homeFlag == 0 && button2 == 0) {          
              analogWrite(14, 100);       
              analogWrite(15, 0);         // drive axis up toward proximity sensor
              homeFlag = 1;
            }

            else if (homeFlag == 1 && prox == 0) {
              analogWrite(14, 0);           // stop motor
              analogWrite(15, 0);
              encoder0Pos = 0;              // zero encoder
              homeFlag = 2;
            }  

            if (prox == 0) {
              encoder0Pos = 0;              // always zero encoder when it hits to the top
            }

            // drive motor

            if (homeFlag == 2) {

                if (demandArmZAccum < encoder0Pos - 50) {
                  analogWrite(14, 0);       
                  analogWrite(15, 100);         // drive axis down
                }
                else if (demandArmZAccum > encoder0Pos + 50) {
                  analogWrite(14, 100);       
                  analogWrite(15, 0);         // drive axis down
                }
    
                else {
                  analogWrite(14, 0);       
                  analogWrite(15, 0);         // stop                             
                }

            }

            // deal with driving wheels

            forward0 = demandx * 83466; // convert m/s into counts/s
            forward1 = demandx * 83466; // convert m/s into counts/s

            turn0 = demandz * 15091;    // convert rads/s into counts/s
            turn1 = demandz * 15091;    // convert rads/s into counts/s

            forward1 = forward1*-1;      // one motor and encoder is mounted facing the other way

            odrive1.SetVelocity(0, forward0 + turn0); 
            odrive1.SetVelocity(1, forward1 + turn1);

            // get positions and velocities from ODrive

            pos0 = (odrive1.GetPosition(1)) *-1;                   
            pos1 = odrive1.GetPosition(0);   

            // work out the difference on each loop, and bookmark the old value
            pos0_diff = pos0 - pos0_old;
            pos1_diff = pos1 - pos1_old;            
            pos0_old = pos0;
            pos1_old = pos1;
    
            // calc mm from encoder counts
            pos0_mm_diff = pos0_diff / 83.44;
            pos1_mm_diff = pos1_diff / 83.44;

            // calc distance travelled based on average of both wheels
            pos_average_mm_diff = (pos0_mm_diff + pos1_mm_diff) / 2;   // difference in each cycle
            pos_total_mm += pos_average_mm_diff;                       // calc total running total distance

            // calc angle or rotation to broadcast with tf
            theta += (pos1_mm_diff - pos0_mm_diff) / 360;
            
            if (theta > PI)
            theta -= TWO_PI;
            if (theta < (-PI))
            theta += TWO_PI;

            // calc x and y to broadcast with tf

            y += pos_average_mm_diff * sin(theta);
            x += pos_average_mm_diff * cos(theta);

            // *** broadcast odom->base_link transform with tf ***

            geometry_msgs::TransformStamped t;           
                      
            t.header.frame_id = odom;
            t.child_frame_id = base_link;
            
            t.transform.translation.x = x/1000;   // convert to metres
            t.transform.translation.y = y/1000;
            t.transform.translation.z = 0;
            
            t.transform.rotation = tf::createQuaternionFromYaw(theta);
            t.header.stamp = nh.now();
                     
            broadcaster.sendTransform(t);

            // *** broadcast base_link->arm transform with tf ***

            geometry_msgs::TransformStamped k;

            k.header.frame_id = base_link;
            k.child_frame_id = arm;

            zArm = 1.0 + ((0.5/50000) * encoder0Pos);            
           
            k.transform.translation.x = (x3/1000)-0.1;  
            k.transform.translation.y = (y3/1000)*-1;
            k.transform.translation.z = zArm; 

            k.transform.rotation = tf::createQuaternionFromYaw(0);

            broadcaster.sendTransform(k);
            k.header.stamp = nh.now();

            // *** broadcast odom message ***

            nav_msgs::Odometry odom_msg;
            odom_msg.header.stamp = nh.now();
            odom_msg.header.frame_id = odom;
            odom_msg.pose.pose.position.x = x/1000;
            odom_msg.pose.pose.position.y = y/1000;
            odom_msg.pose.pose.position.z = 0.0;
            odom_msg.pose.pose.orientation = tf::createQuaternionFromYaw(theta);

            odom_msg.child_frame_id = base_link;
            odom_msg.twist.twist.linear.x = ((pos0_mm_diff + pos1_mm_diff) / 2)/10;          // forward linear velovity
            odom_msg.twist.twist.linear.y = 0.0;                                            // robot does not move sideways
            odom_msg.twist.twist.angular.z = ((pos1_mm_diff - pos0_mm_diff) / 360)*100;      // anglular velocity

            odom_pub.publish(&odom_msg);

            // Arm Control

            // unfold        

            if (fold == 1 && foldFlag == 0) {
                pos30 = 126;
                foldFlag = 1;
                previousFoldMillis = currentMillis;          
            }
            else if (fold == 1 && foldFlag == 1 && currentMillis - previousFoldMillis >= 1000) {
                pos10 = 45;
                pos20 = 135;
                foldFlag = 2;
                previousFoldMillis = currentMillis;
            }
            else if (fold == 1 && foldFlag == 2 && currentMillis - previousFoldMillis >= 2000) {
                // wait for unfold
                foldFlag = 0;
                fold = 5;
            }
    
            // fold
    
            if (fold == 0 && foldFlag == 0) {
                pos10 = 0;
                pos30 = 126;
                foldFlag = 1;
                previousFoldMillis = currentMillis; 
            }
    
            else if (fold == 0 && foldFlag == 1 && currentMillis - previousFoldMillis >= 1000) {
                pos10 = 0;
                pos20 = 90;
                foldFlag = 2;
                previousFoldMillis = currentMillis;
            }
            
            else if (fold == 0 && foldFlag == 2 && currentMillis - previousFoldMillis >= 1000) {
                pos30 = 90;
                foldFlag = 0;
                fold = 2;
            }

            // arm data hendling and kinematics

            Serial6.print(armX);      // Vector3 messages received
            Serial6.print(" , ");
            Serial6.print(armY);
            Serial6.print(" , ");
            Serial6.print(armZ);  
            Serial6.print(" *** ");     
            Serial6.print(x3);
            Serial6.print(" , ");
            Serial6.print(y3);
            Serial6.print(" , ");
            Serial6.print(demandArmZAccum);

            Serial6.println();
                 

            //demandArmXAccum = demandArmXAccum + (demandArmX * 10);   /// add or subtract to the value on each cycle.
            //demandArmXAccum = constrain(demandArmXAccum,-300,300);
            //x3 = map(demandArmXAccum, -300,300,580,350);
            x3 = armX;    // use Vector3 message from vision/depth instead
            x3 = constrain(x3,350,580);

            //demandArmYAccum = demandArmYAccum + (demandArmY * 10);   /// add or subtract to the value on each cycle.
            //y3 = constrain(demandArmYAccum,-300,300);
            y3 = armY;    // use Vector3 message from vision/depth instead
            y3 = constrain(y3,-300,300);

            if (fold == 5) {        // only run kinematics if arm is folded out
    
                  //dxl.writeControlTableItem(PROFILE_VELOCITY, 10, 60);
                  //dxl.writeControlTableItem(PROFILE_VELOCITY, 20, 60);
                  //dxl.writeControlTableItem(PROFILE_VELOCITY, 30, 60);
                  //dxl.writeControlTableItem(PROFILE_VELOCITY, 40, 60);
    
                  // calculate modification to shoulder angle and arm length
          
                  shoulderAngle2a = atan(y3/x3);
                  shoulderAngle2aDegrees = shoulderAngle2a * (180/PI);    // degrees
    
                  x2 = x3/cos(shoulderAngle2a);
    
                  // calculate arm length based on lower arm / upper arm length and elbow and shoulder angle
                  shoulderAngle1a = (sq(upperLength) + sq(x2) - sq(lowerLength)) / (2 * upperLength * x2);
                  shoulderAngle1 = acos(shoulderAngle1a);     // radians
                  elbowAngle1a = (sq(upperLength) + sq(lowerLength) - sq(x2)) / (2 * upperLength * lowerLength);
                  elbowAngle1 = acos(elbowAngle1a);     // radians
              
                  // calc degrees from angles
                  shoulderAngle1Degrees = shoulderAngle1 * (180/PI);    // degrees
                  elbowAngle1Degrees = elbowAngle1 * (180/PI);              // degrees      
          
                  pos10 = shoulderAngle1Degrees + shoulderAngle2aDegrees;
                  pos20 = elbowAngle1Degrees + 27;  // add on the offset cuased by the lower two sections of the arm being at 45'
    
                  pos40 = (270 - ((shoulderAngle1Degrees + shoulderAngle2aDegrees) + (elbowAngle1Degrees+27) + 126))*-1;
    
            }   // end of kinematics 

            // control the Eye tilt

            demandEyeAccum = demandEyeAccum + (demandEye * 10);   // add or subtract to the value on each cycle.
            demandEyeAccum = constrain(demandEyeAccum,-300,300);

            pos50 = map(demandEyeAccum,-300,300,-90,90);                     // constrain to the limits we want the eye to turn in degrees
            
            // constrain joints so we can't break the robot
            
            pos10 = constrain(pos10,0,90);
            pos20 = constrain(pos20,90,180);
            pos30 = constrain(pos30,90,180);
            pos40 = constrain(pos40,-90,90);
            pos50 = constrain(pos50,-90,90);
       
            //turn all the joints around so we can give the joint the actual angle, taking into account the servo offsets for default positions.
          
            finPos10 = offset10 + pos10;
            finPos20 = offset20 + (180-pos20);
            finPos30 = offset30 - (180-pos30);
            finPos40 = offset40 + pos40;
            finPos50 = offset50 + pos50;

          
            // write the joint positions to the servos, but only if they change.
            // the ROSserial library needs lots of time or it times out, so we keep other things to a minimum.

            if (finPos10 != finPos10Prev) {          
              dxl.setGoalPosition(10, finPos10, UNIT_DEGREE);
            }

            if (finPos20 != finPos20Prev) {          
              dxl.setGoalPosition(20, finPos20, UNIT_DEGREE);
            }

            if (finPos30 != finPos30Prev) {          
              dxl.setGoalPosition(30, finPos30, UNIT_DEGREE);
            }

            if (finPos40 != finPos40Prev) {          
              dxl.setGoalPosition(40, finPos40, UNIT_DEGREE);
            }

            if (finPos50 != finPos50Prev) {          
              dxl.setGoalPosition(50, finPos50, UNIT_DEGREE);
            }

            // bookmark previous values so we know if they changed

            finPos10Prev = finPos10;
            finPos20Prev = finPos20;
            finPos30Prev = finPos30;
            finPos40Prev = finPos40;
            finPos50Prev = finPos50;

            // publish eye angle as a ROStopic/message

            pos50Pub = dxl.getPresentPosition(50, UNIT_DEGREE);   // read actual angle from servo

            pos50Pub = map(pos50Pub,90,270,180,0);
            eye_msg.data = pos50Pub;
            pub_eye.publish(&eye_msg);                            // publish as ROS message



        } // end of timed loop

} // end of main loop


void doEncoderA(){  

  // look for a low-to-high on channel A
  if (digitalRead(encoder0PinA) == HIGH) { 
    // check channel B to see which way encoder is turning
    if (digitalRead(encoder0PinB) == LOW) {  
      encoder0Pos = encoder0Pos + 1;         // CW
    } 
    else {
      encoder0Pos = encoder0Pos - 1;         // CCW
    }
  }
  else   // must be a high-to-low edge on channel A                                       
  { 
    // check channel B to see which way encoder is turning  
    if (digitalRead(encoder0PinB) == HIGH) {   
      encoder0Pos = encoder0Pos + 1;          // CW
    } 
    else {
      encoder0Pos = encoder0Pos - 1;          // CCW
    }
  }
 
}

void doEncoderB(){  

  // look for a low-to-high on channel B
  if (digitalRead(encoder0PinB) == HIGH) {   
   // check channel A to see which way encoder is turning
    if (digitalRead(encoder0PinA) == HIGH) {  
      encoder0Pos = encoder0Pos + 1;         // CW
    } 
    else {
      encoder0Pos = encoder0Pos - 1;         // CCW
    }
  }
  // Look for a high-to-low on channel B
  else { 
    // check channel B to see which way encoder is turning  
    if (digitalRead(encoder0PinA) == LOW) {   
      encoder0Pos = encoder0Pos + 1;          // CW
    } 
    else {
      encoder0Pos = encoder0Pos - 1;          // CCW
    }
  }
  

}

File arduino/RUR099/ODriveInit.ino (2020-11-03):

// init hips

void OdriveInit1() {

          //Serial1 << "w axis" << axis << ".controller.config.vel_limit " << 60000.0f << '\n';
          //Serial1 << "w axis" << axis << ".motor.config.current_lim " << 20.0f << '\n';
          //Serial1 << "w axis" << axis << ".motor.config.calibration_current " << 10.0f << '\n';

          // *** current limit and other parameers are set on the ODrive using the Odrive tool as above. *** 

          // init ODrive axis

          //axis 0

          requested_state = ODriveArduino::AXIS_STATE_MOTOR_CALIBRATION;
          odrive1.run_state(0, requested_state, true);
    
          requested_state = ODriveArduino::AXIS_STATE_ENCODER_OFFSET_CALIBRATION;
          odrive1.run_state(0, requested_state, true);
    
          requested_state = ODriveArduino::AXIS_STATE_CLOSED_LOOP_CONTROL;
          odrive1.run_state(0, requested_state, false); // don't wait 

          //axis 1

          requested_state = ODriveArduino::AXIS_STATE_MOTOR_CALIBRATION;
          odrive1.run_state(1, requested_state, true);
    
          requested_state = ODriveArduino::AXIS_STATE_ENCODER_OFFSET_CALIBRATION;
          odrive1.run_state(1, requested_state, true);
    
          requested_state = ODriveArduino::AXIS_STATE_CLOSED_LOOP_CONTROL;
          odrive1.run_state(1, requested_state, false); // don't wait 
               
}

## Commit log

2020-10-13 Initial base design
    [MotorPulley.stl, RUR_001.stp, WheelPulley.stl]
2020-11-03 Added ROS / Arduino files
    [rur.urdf]
2020-12-15 Addition of head assembly
2021-01-21 added detailed description files
    [back_caster.stl, base_link.stl, camera_link.stl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]
2021-03-19 Added ROS serial stuff & arm
2021-03-19 Added Arm and housing
2021-05-24 Added LiDAR plugin
2021-05-27 added eye servo assembly
2021-05-27 Added Intel Realsense / Jetson vision
2021-06-20 Added model colour in RViz
    [materials.xacro, rur_detailed.xacro]
2021-06-20 added house model and world
    [model.sdf]
2021-06-20 Made navigation work with simulation
    [rur_detailed.xacro]
2021-06-24 solved gazebo blacking problem - added models
    [model-1_2.sdf, model-1_3.sdf, model-1_4.sdf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]
